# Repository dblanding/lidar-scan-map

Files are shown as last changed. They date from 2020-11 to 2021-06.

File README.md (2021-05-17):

## Mapping LiDAR scan data
This project uses a Benewake TFMini Plus LiDAR module mounted to scan 225 degrees on a vertical axis. A hall effect angle encoder reports the angular position of the scan rotor.

### Rotating LiDAR mounted on a Zero Turn (early prototype) car:
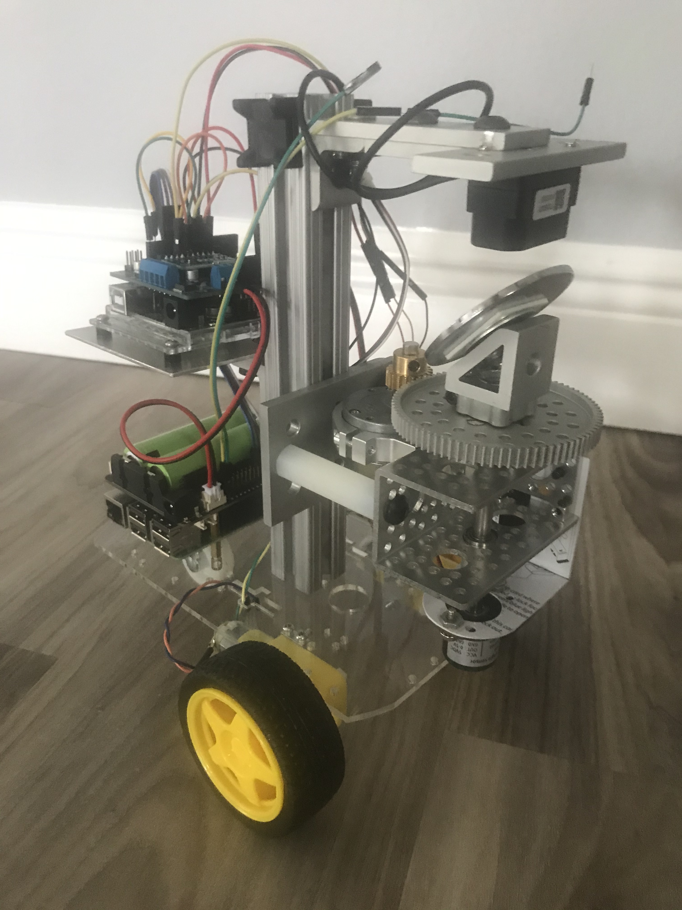
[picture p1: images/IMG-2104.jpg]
Zero Turn Car with rotating LiDAR


### Rotating LiDAR mounted on an Omni-Wheel type car:
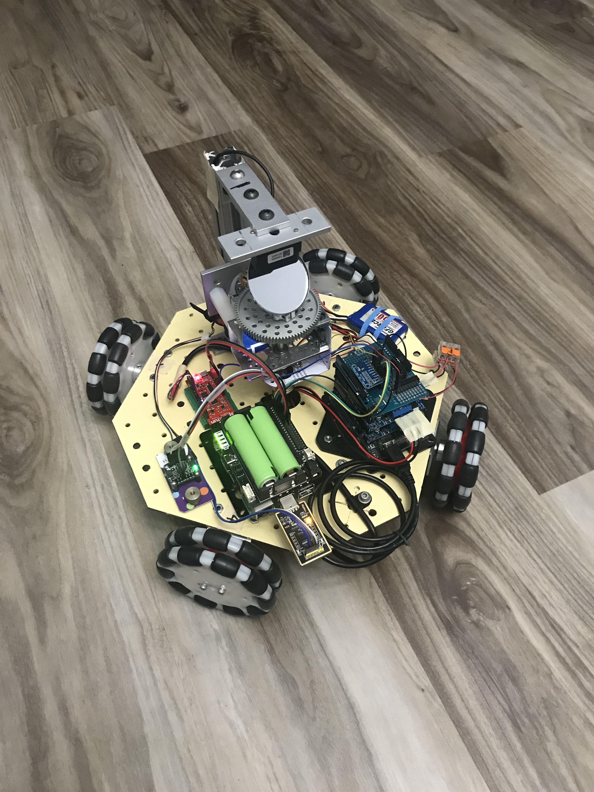
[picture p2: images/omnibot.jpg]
Omni Wheel Car with rotating LiDAR


More about **Omni-Wheels** can be found [here](omni-wheels.md).

By using the scan data, the car can navigate autonomously,
able to make a [multi-leg trip](docs/triplog-21-05-16-06-00/trip_log.md) through the house.  
An onboard Raspberry Pi 3B+ runs a python program which:  
* Collects data from the TFminiPlus on a USB serial port
* Collects readings from the angular encoder via ADC (on I2C bus)
* Finds the best fit lines through the scan points
* Displays a plot of the points and the best fit lines.
* Using OpenCV, calculates the best path forward, avoiding objects in its environment
* Sends motor drive commands to the Arduino on the serial port  
  (Arduino controls the motors through an Adafruit motor shield)
* Keeps track of its position using data from an IMU and an odometer.
  * The IMU is an Adafruit BNO085 operating in RVC mode, sending data via serial
  * The odometer is a wheel mounted on the shaft of an incremental encoder,
    * Encoder data is collected by an ESP32 and sent to RasPi via ADC

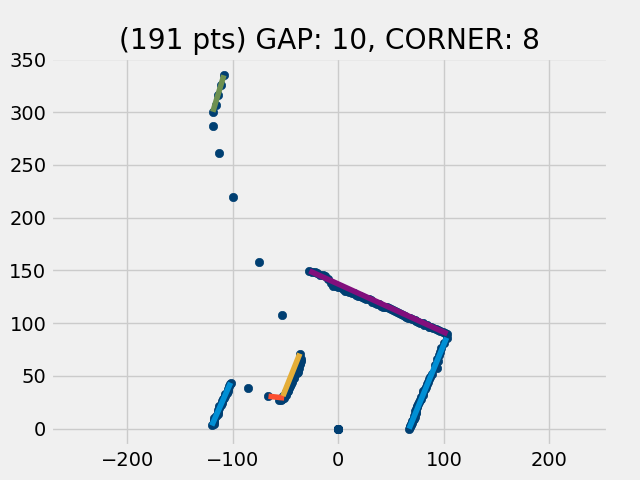
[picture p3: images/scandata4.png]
plot showing data points & best-fit lines


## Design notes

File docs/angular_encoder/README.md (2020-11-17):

### Investigate use of ADS1115 ADC to collect angle encoder data

Started with [Adafruit ADS1x15 Library](https://learn.adafruit.com/raspberry-pi-analog-to-digital-converters/ads1015-slash-ads1115) to convert 0-5v signal from angle encoder to digital value and send it to the RasPi via I2C bus. This worked quite well. The Python program ads1115speedTest.py shows that encoder values can be received at rates easily exceeding the 100Hz speed of the TFminiPlus.
#### Calibration:

I conducted a calibration procedure in which the angle encoder was positioned at 90, 180, and 270 degrees. (Actually, I hooked up a meter to the output of the encoder and positioned it at 1.25V, 2.5V, and 3.75V) then used the python prgogram to get the encoder value.)
Along the way, I discovered a couple of  things:
* >One problem I discovered was that different 5V power supplies are not always exactly 5V.
When the Geekworm X728 UPS is plugged in and charging, the RasPi 5V level goes to 5.25V.
When it's unplugged it drops to more nearly 5V.
If an Arduino is hooked to the RasPi by USB, The Arduino 5V level is similarly affected, but not as severly. It goes from 5.1V when the X728 is charging to 4.95V when the charger is unplugged. 
* >I chose to use the Arduino power supply because it is the best one available. The [ADS1115 datasheet](https://cdn-shop.adafruit.com/datasheets/ads1115.pdf) explains that at its default settings, it converts a voltage between -4.096V and +4.096V to a number that ranges from -32768 to 32767. With these default settings, useful values are gotten in the desired angular range (90 degrees to 270 degrees).
* >Using the Arduino 5V supply (and with the charger unplugged) I manually moved the rotor to each of 3 positions: 1.25V, 2.50V, 3.75V and recorded the corresponding encoder count value. To achieve the best agreement between the measured encoder count value and the calculated encoder count value, I ended up fudging the 4.096 number to 4.115. See Excel file ang_encdr_calibr.xlsx  
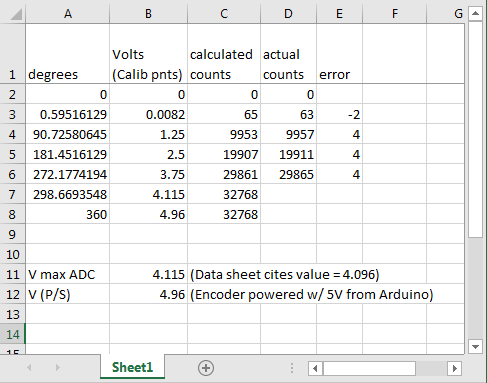
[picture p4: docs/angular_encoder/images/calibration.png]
Excel sprreadsheet


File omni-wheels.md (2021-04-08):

## OMNI-WHEEL CAR

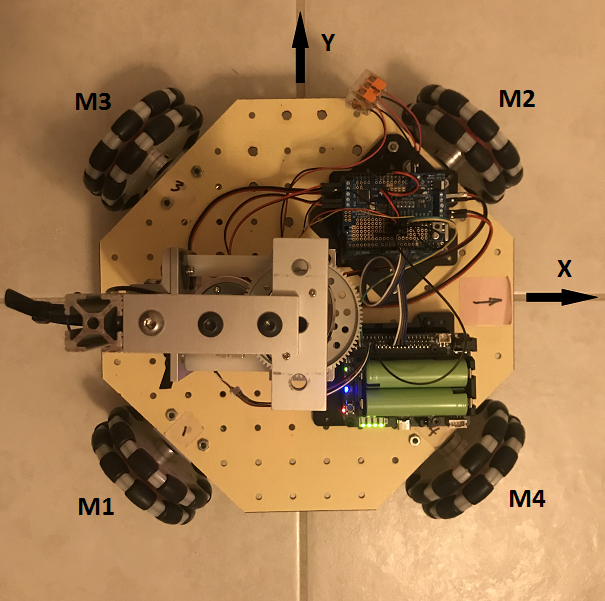
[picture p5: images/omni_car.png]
omni-wheel car


### Top view of Omni Wheel car showing wheel/motors and directional conventions

This configuration of omni-wheels is easily controlled to move in any direction: X, Y, θz:
- forward-back motion (along the X axis)
- right-left sideways motion (along the Y axis)
- spin motion (θz).

Moreover, all three of these motions can be superimposed. The motors can be commanded to combine these motions simultaneously. (More about that later.) For now, let's just consider how we can get the car to move in one DOF at a time.

Imagine that we want to drive the car along a -45 degree direction into the fourth quadrant (along the common axis of wheel motors M3 and M4). Only wheel motors **M1 and M2** would run. **M1** would need to be driven **clockwise** and **M2** would need to be driven **CCW** at the same speed. Wheel motors M3 and M4 would not run. To drive drive the car at speed S along the 45 degree direction, we would send the following drive values to the motors:

```
m1 = +S
m2 = -S
m3 = 0
m4 = 0
```

Now imagine that we want to drive the car along a +45 degree direction into the first quadrant (along the common axis of wheel motors M1 and M2). Only wheel motors **M3 and M4** would run. **M4** would need to be driven **clockwise** and **M3** would need to be driven **CCW** at the same speed. Wheel motors M1 and M2 would not run. To drive drive the car at speed S along the 135 degree direction, we would send the following drive values to the motors:

```
m1 = 0
m2 = 0
m3 = -S
m4 = +S
```

Notice that the car's motion along the -45 degree direction is completely **independent** from its motion along the **orthogonal** +45 degree direction. First, it suggests that the "natural coordinate system" for the omni-wheels runs through the wheel axes (which happens to be oblique to the car's coordinate system). But it also invites us to realize that we may combine the control of these two **independent degrees of freedom** in any combination we desire. Thus, it seems reasonable to consider driving the car in any arbitrary angular direction. The mathematics of this is simplified by using **polar coordinates (r, θ)** to specify the speed and direction of the car. To convert between the omni-wheels 'natural' coordinates and the car's coordinates, we simply add or subtract 45 degrees (pi/4) from the theta value. Below is the algorithm to drive the car in a direction theta at speed.

```
speed, theta = desired_speed_and_direction
theta -= pi/4
u, v = convert_polar_to_rect(speed, theta)
m1 = u
m2 = -u
m3 = -v
m4 = v
```
Notice the rectangular coordinates in the omni-wheel's natural coordinate system have been labeled u, v. This is intended to remind us that they are not the same as x, y coordinates in the car's coordinate system.
If we want to simultaneously spin the car **CCW** about its own Z axis, all four wheel motors would receive an additional **CW** component as shown below.
```
spin = some_value
speed, theta  = desired_speed_and_direction
theta -= pi/4
u, v = convert_polar_to_rect(speed, theta)
m1 = u + spin
m2 = -u + spin
m3 = -v + spin
m4 = v + spin
```

### Maintaining Cross-Track position within travel lane

Let's say we want our omni-wheel car to travel forwrd (FWD) in the positve X direction and we want it to stay centered in its travel lane. Just like any car, it is neccesary to make subtle steering corrections in response to unintended cross-track deviations from its intended path. In the figure below, our car has been shown in a 'travel lane' traveling from left to right. 

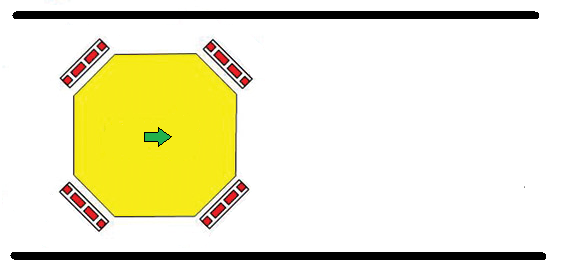
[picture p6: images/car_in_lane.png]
car in lane


This is where polar coordinates again come to the rescue. It's easy to make a subtle steering correction if we're already working in polar coordinates. Simply modulate the angle coordinate until the car's cross-track position error has been nulled. Done!
Below is shown the signature of the method to drive the car using polar coordinates. 

``` python
    def go(self, speed, angle, spin=0):
        """
		Drive at speed (int) in relative direction angle (degrees)
        while simultaneoulsy spinning CCW at rate = spin (int).
        """
```

### Making radius turns

What if the lane is curved? How do we make the car follow a curved path of radius = R as shown in the diagram below? That's what the spin parameter is for.

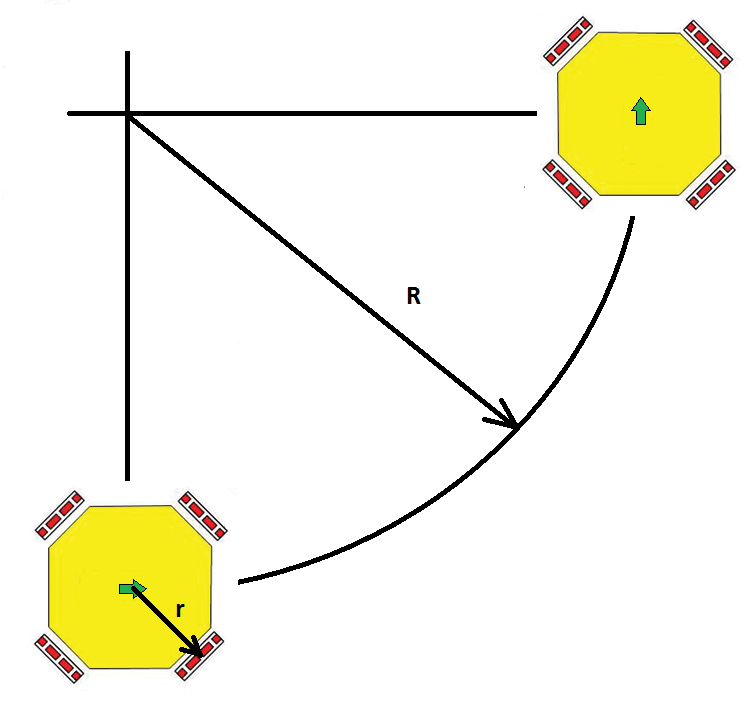
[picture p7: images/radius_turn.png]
curved path


This diagram shows our car moving in the FWD direction while simultaneously spinning CCW, resulting in a path which is the arc of a circle of radius R. We need to come up with the correct value of spin which will produce 90 degrees of rotation as the car translates along 1/4 of the circumference of the circle.

Notice that the drive direction of the wheels is 45 degrees from the direction of travel of the car. As a result, the motion of the wheels at their interface with the floor must **exceed** the distance the car translates by a factor of √2.

> translation distance (at wheels) = (pi * R/2) * √2

Knowing the dimension r from the car's geometric center to each wheel, we can find the corresponding value of spin that will produce 90 degrees of CCW rotation of the car about its own axis is:

> spin distance (at wheels) = pi * r/2

In summary, the car will follow the curved path of radius R if the value of spin is proportional to the car speed in the following ratio:

> spin_ratio =  r/R * √2/2

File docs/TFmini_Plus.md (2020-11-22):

## TF Mini / TF Mini Plus resources

[Benewake website](http://en.benewake.com/)

### TF Mini

The TFmini is available in two different comm. configurations: I2C & Serial.
The one I have is the Serial type and cannot work in I2C mode.

[Instructables (Complete guide)](https://www.instructables.com/Benewake-LiDAR-TFmini-Complete-Guide/)

[Sparkfun tutorial (I2C)](https://learn.sparkfun.com/tutorials/tfmini---micro-lidar-module-qwiic-hookup-guide)

[Sparkfun tutorial (UART)](https://learn.sparkfun.com/tutorials/tfmini---micro-lidar-module-hookup-guide)

### TF Mini Plus

The TFMini-Plus works optionally in either serial or I2C mode.

[Benewake TFmini_Plus README](https://github.com/TFmini/TFmini-Plus/blob/master/README.md)

[Arduino library for TFMini-Plus using I2C interface](https://github.com/budryerson/TFMini-Plus-I2C)

[Medium article: Interfacing TFmini Plus LiDAR with Raspberry Pi](https://medium.com/@engribrahimqazi/interfacing-tfmini-plus-lidar-with-raspberry-pi-4b-6cd82fcca5f1)

> This last article led me to discover that the TF Mini can send its data directly to the RasPi Python program. No need for an Arduino.  
Instead of using the Arduino to interface with the lidar and then send the data to my python program over the serial bus, I should allow the Python program to interface directly with the TFmini Plus. I took the code in the article and modified it so it doesn't waste time printing, but just collects data as fast as it arrives on the serial port.

```
# -*- coding: utf-8 -*
"""from 'Interfacing TFmini Plus LiDAR with Raspberry Pi 4B' by Ibrahim Qazi
https://medium.com/@engribrahimqazi/interfacing-tfmini-plus-lidar-with-raspberry-pi-4b-6cd82fcca5f1

Needed to enable serial through gpio pins by doing the following:
First: sudo raspi-config, Interfacing Options, then Serial,
select No for the login shell and Yes for the serial port hardware to be enabled.
Afterwards, reboot.
Change serial device from "/dev/ttyAMA0" to "/dev/ttyS0".
"""

import time
import serial

ser = serial.Serial("/dev/ttyS0", 115200)

def read_data():
    """Read data from Benewake TFmini Plus LiDAR and print it"""
    last_time = time.time()
    data = []
    while len(data) < 100:
        counter = ser.in_waiting # count the number of bytes of the serial port
        if counter > 8:
            bytes_serial = ser.read(9)
            
            if bytes_serial[0] == 0x59 and bytes_serial[1] == 0x59:
                distance = bytes_serial[2] + bytes_serial[3]*256
                strength = bytes_serial[4] + bytes_serial[5]*256
                temperature = bytes_serial[6] + bytes_serial[7]*256
                temperature = (temperature/8) - 256
                now = time.time()
                strline = "%s, %s, %s, %s, %s\n" % (counter, distance, strength,
                                                    temperature, now - last_time)
                data.append(strline)
                last_time = now
    with open('tfminiPlus_data', 'w') as f:
        print(len(data))
        f.writelines(data)

if __name__ == "__main__":
    if ser.isOpen() == False:
        ser.open()
    read_data()
```

Examination of the output file, shows that a read occurs as soon as 9 bytes are queued up and waiting on the serial port.  
Also, the elapsed time since the previous read hovers right around 10 mSec, so the device really does operate at 100 Hz, as advertised. 

Bytes waiting, distance, strength, temperature, time since last read

```
9, 28, 5812, 60.0, 0.001964092254638672
9, 28, 5814, 60.0, 0.010060310363769531
9, 28, 5815, 60.0, 0.010145902633666992
9, 28, 5821, 60.0, 0.010141611099243164
9, 28, 5813, 60.0, 0.010251522064208984
9, 28, 5818, 60.0, 0.010085821151733398
9, 28, 5818, 60.0, 0.010092496871948242
9, 28, 5819, 60.0, 0.010134696960449219
9, 28, 5816, 60.0, 0.010140180587768555
9, 28, 5812, 60.0, 0.010195255279541016
9, 28, 5821, 60.0, 0.010090112686157227
...
```

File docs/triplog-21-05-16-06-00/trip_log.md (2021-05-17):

## Log for Trip started Sun May 16 06:00:17 2021.  
  
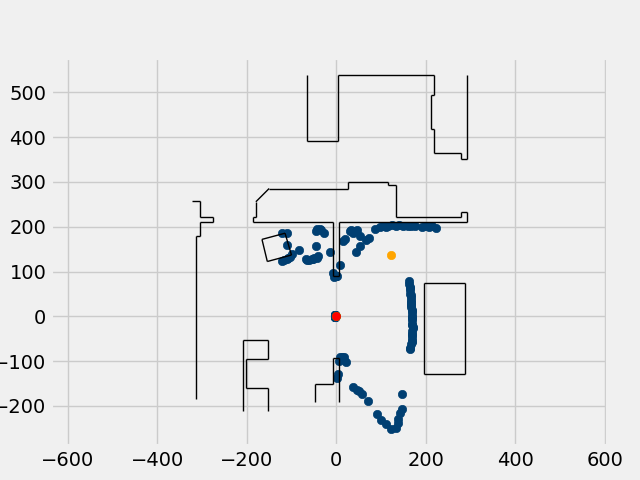
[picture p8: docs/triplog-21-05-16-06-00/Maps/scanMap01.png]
Map Plot 01
  
Leg 1  
Starting Coords: (0, 0)  
Turning Left 48.0 deg to heading -48.01  
Heading after turn: -48.57 deg.  
Distance to target: 184.0 cm.  
Distance driven: 176 cm.  
Heading after drive: -48.230000000000004 deg.  
Ending Coords: (118, 130)  
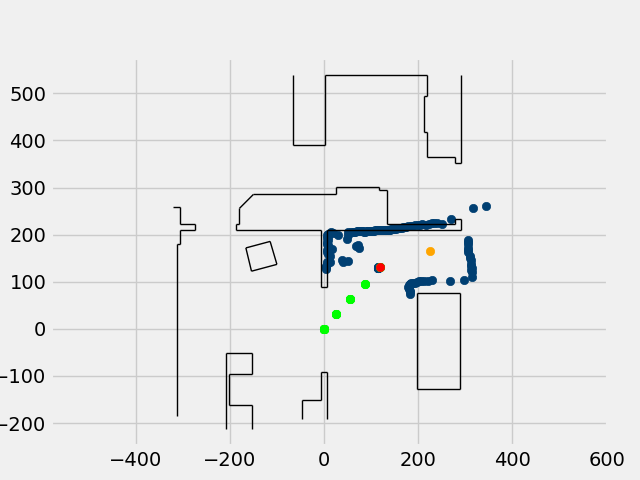
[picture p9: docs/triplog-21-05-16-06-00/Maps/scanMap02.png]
Map Plot 02
  
Leg 2  
Starting Coords: (118, 130)  
Turning Right 29.999999999999996 deg to heading -18.250000000000004  
Heading after turn: -16.65 deg.  
Distance to target: 112.0 cm.  
Distance driven: 115 cm.  
Heading after drive: -13.56 deg.  
Ending Coords: (228, 163)  
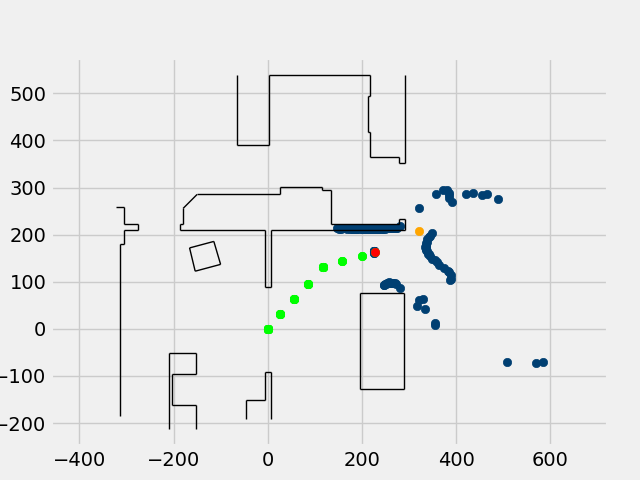
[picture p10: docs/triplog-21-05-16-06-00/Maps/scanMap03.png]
Map Plot 03
  
Leg 3  
Starting Coords: (228, 163)  
Turning Left 11.999999999999998 deg to heading -25.57  
Heading after turn: -23.740000000000002 deg.  
Distance to target: 103.0 cm.  
Distance driven: 103 cm.  
Heading after drive: -21.94 deg.  
Ending Coords: (322, 205)  
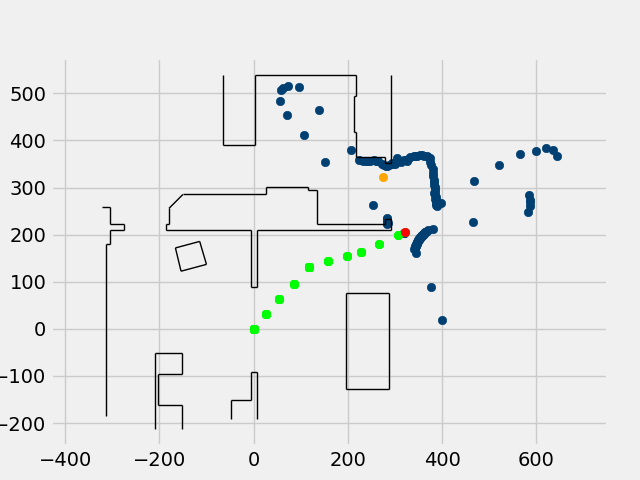
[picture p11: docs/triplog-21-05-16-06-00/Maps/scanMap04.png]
Map Plot 04
  
Leg 4  
Starting Coords: (322, 205)  
Turning Left 90.0 deg to heading -111.94  
Heading after turn: -108.47 deg.  
Distance to target: 127.0 cm.  
Distance driven: 129 cm.  
Heading after drive: -108.81 deg.  
Ending Coords: (279, 326)  
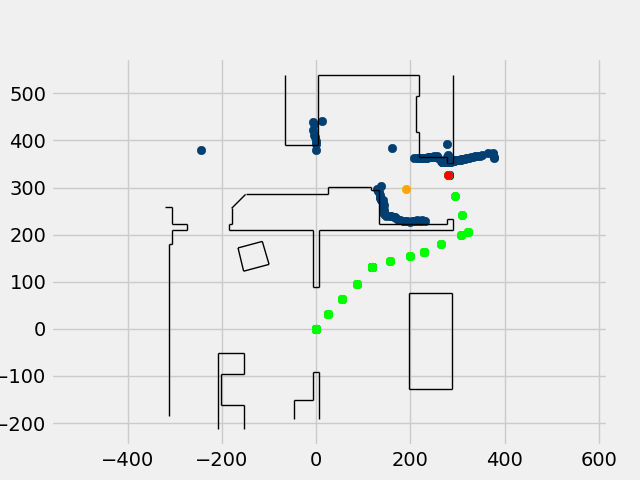
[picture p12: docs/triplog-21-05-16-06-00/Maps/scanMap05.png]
Map Plot 05
  
Leg 5  
Starting Coords: (279, 326)  
Turning Left 90.0 deg to heading -198.79000000000002  
Heading after turn: 161.45000000000002 deg.  
Distance to target: 94.0 cm.  
Distance driven: 84 cm.  
Heading after drive: 161.48 deg.  
Ending Coords: (201, 297)  
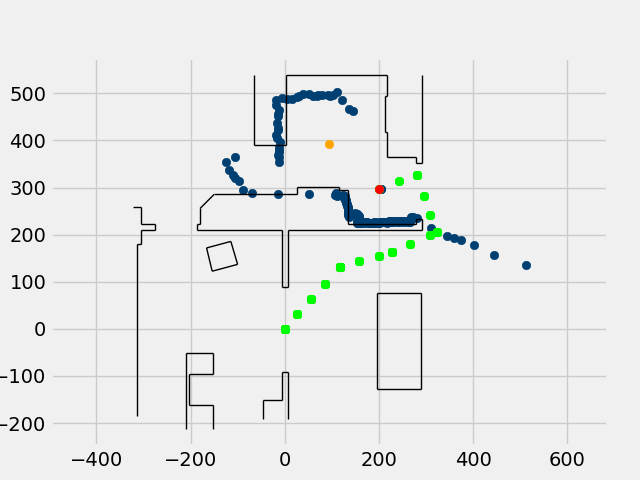
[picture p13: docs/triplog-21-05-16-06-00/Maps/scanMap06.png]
Map Plot 06
  
Leg 6  
Starting Coords: (201, 297)  
Turning Right 59.99999999999999 deg to heading 221.5  
Heading after turn: -140.25 deg.  
Distance to target: 142.0 cm.  
Distance driven: 143 cm.  
Heading after drive: -137.70000000000002 deg.  
Ending Coords: (91, 389)  
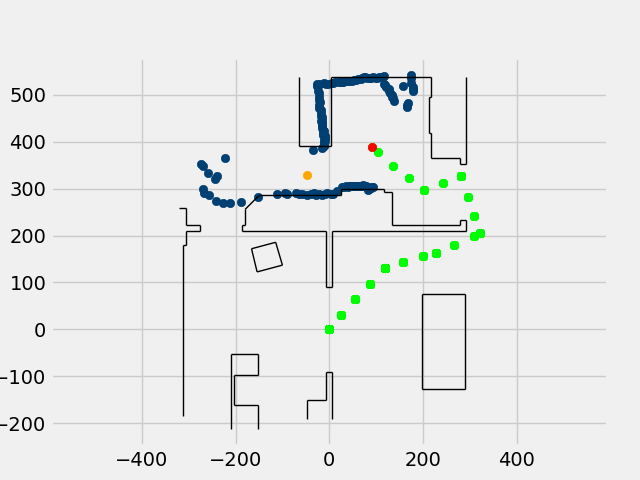
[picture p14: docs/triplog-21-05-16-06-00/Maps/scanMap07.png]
Map Plot 07
  
Leg 7  
Starting Coords: (91, 389)  
Turning Left 66.0 deg to heading -203.66  
Heading after turn: 156.94 deg.  
Distance to target: 152.0 cm.  
Distance driven: 146 cm.  
Heading after drive: 158.76 deg.  
Ending Coords: (-40, 326)  
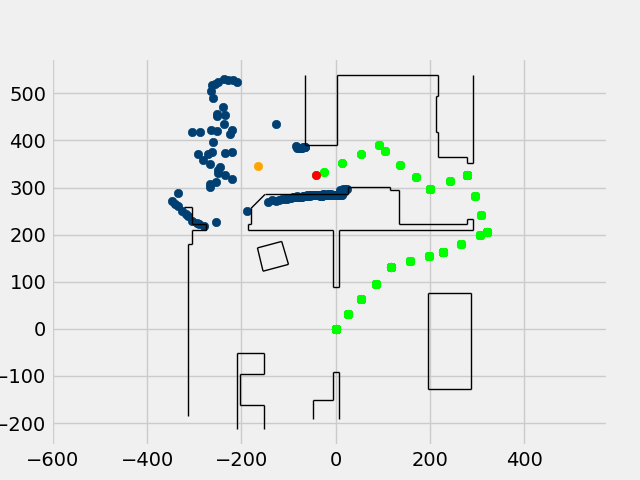
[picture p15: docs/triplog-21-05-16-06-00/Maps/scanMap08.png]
Map Plot 08
  
Leg 8  
Starting Coords: (-40, 326)  
Turning Right 29.999999999999996 deg to heading 188.75  
Heading after turn: -173.33 deg.  
Distance to target: 125.0 cm.  
Distance driven: 128 cm.  
Heading after drive: -170.89000000000001 deg.  
Ending Coords: (-167, 342)  
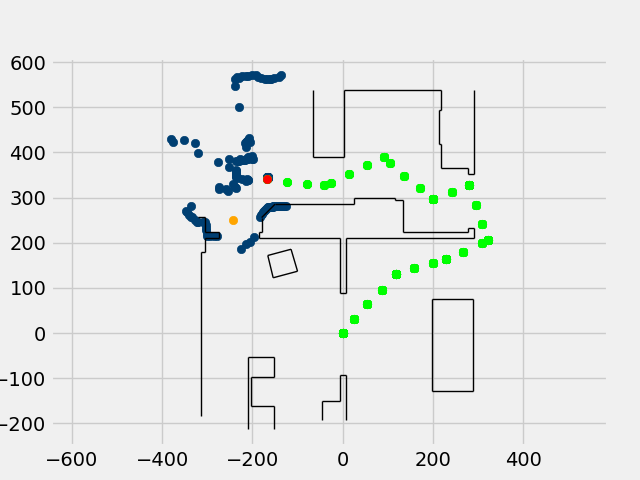
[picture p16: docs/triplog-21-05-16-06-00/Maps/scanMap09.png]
Map Plot 09
  
Leg 9  
Starting Coords: (-167, 342)  
Turning Left 59.99999999999999 deg to heading -230.86  
Heading after turn: 131.03 deg.  
Distance to target: 118.0 cm.  
Distance driven: 117 cm.  
Heading after drive: 129.8 deg.  
Ending Coords: (-242, 251)  
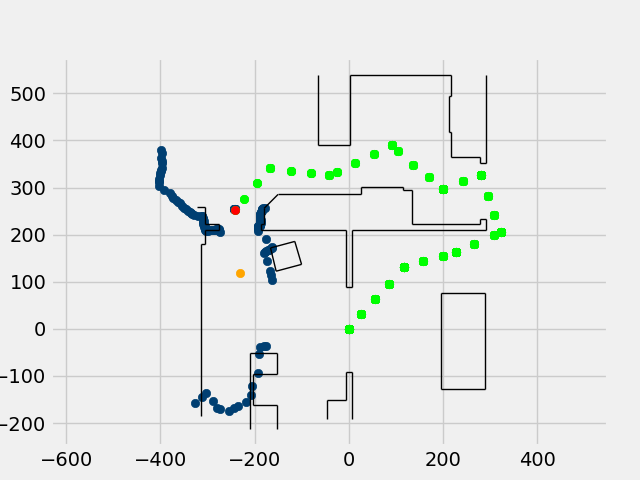
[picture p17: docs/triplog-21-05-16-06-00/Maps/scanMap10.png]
Map Plot 10
  
Leg 10  
Starting Coords: (-242, 251)  
Turning Left 45.0 deg to heading 84.81  
Heading after turn: 88.05 deg.  
Distance to target: 134.0 cm.  
Distance driven: 130 cm.  
Heading after drive: 86.9 deg.  
Ending Coords: (-234, 121)  
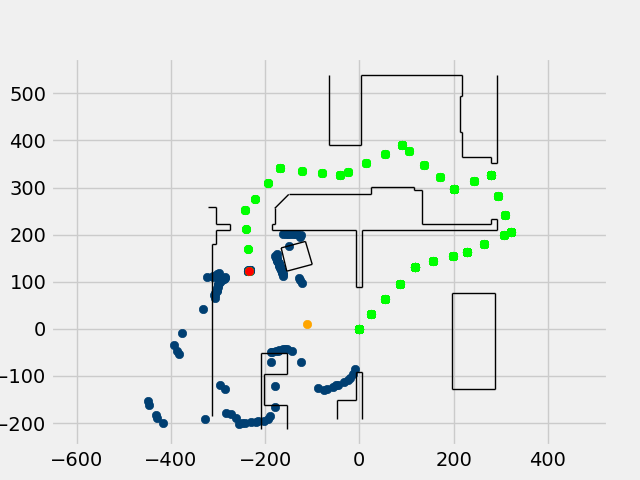
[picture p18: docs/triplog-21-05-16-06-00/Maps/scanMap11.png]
Map Plot 11
  
Leg 11  
Starting Coords: (-234, 121)  
Turning Left 45.0 deg to heading 41.900000000000006  
Heading after turn: 42.5 deg.  
Distance to target: 166.0 cm.  
Distance driven: 164 cm.  
Heading after drive: 44.27 deg.  
Ending Coords: (-112, 11)  
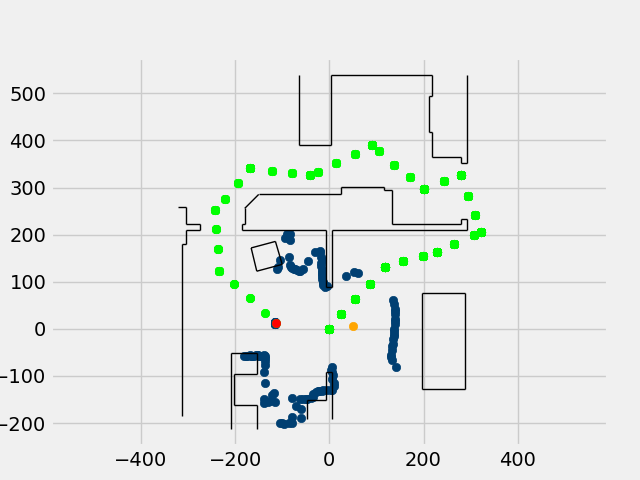
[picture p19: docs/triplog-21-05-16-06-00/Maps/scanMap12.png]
Map Plot 12
  
Leg 12  
Starting Coords: (-112, 11)  
Turning Left 42.0 deg to heading 2.240000000000002  
Heading after turn: 1.0 deg.  
Distance to target: 164.0 cm.  
Distance driven: 161 cm.  
Heading after drive: 1.02 deg.  
Ending Coords: (48, 15)  
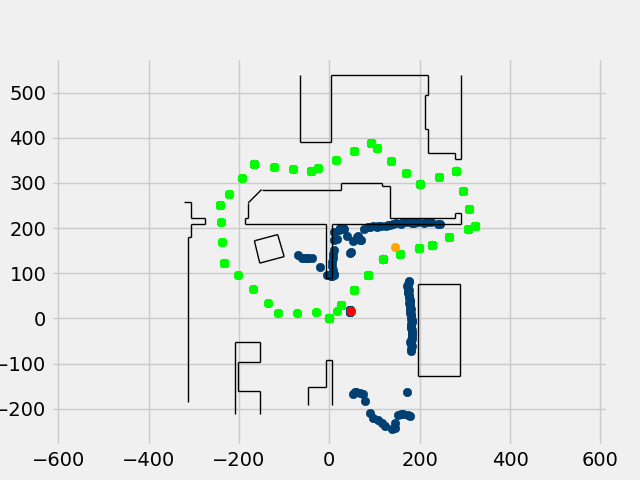
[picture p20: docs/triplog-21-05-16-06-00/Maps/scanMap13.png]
Map Plot 13
  
Leg 13  
Starting Coords: (48, 15)

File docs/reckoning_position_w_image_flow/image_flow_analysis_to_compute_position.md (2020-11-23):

## Can image flow analysis of consecutive scans be used instead of encoders to keep track of robot position?
### 11/23/2020
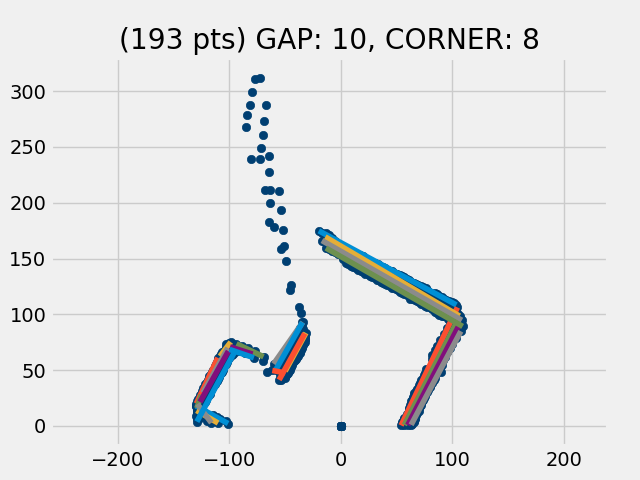
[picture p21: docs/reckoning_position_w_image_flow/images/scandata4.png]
robot moved through 4 positions separated by 2 in


The image above shows 4 scans overlayed as the robot is advanced through 4 positions along the Y axis spaced roughly 2 inches apart. The units on the X and Y axes are in cm, by the way.

The question is: Can we do an **image flow analysis** (similar to the way an optical mouse works) to make a reasonable calculation of the change in the robot's position as it advances from one position to the next.

It looks as though it should be possible. This would simplify the robot as it would be unneccesary to keep track of its position using the usual encoders and/or stepper motors.

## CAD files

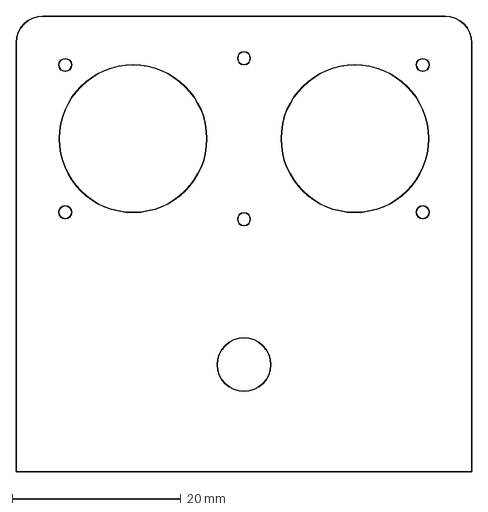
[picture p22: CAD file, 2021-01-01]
CAD/HC-SR04_CC_mnt.dxf
53.9 x 54.0 mm

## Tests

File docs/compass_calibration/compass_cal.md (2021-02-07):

## Compass Calibration

I wanted to see if the uncorrected data I was getting from the HMC5883L device on the robot was in good agreemeent with the compass app on my phone. It wasn't. Here is what I found just looking at the cardinal directions:

Device	 | North | East | South | West
-------- | ----- | ---- | ----- | ----
TRUE     |   0   |  90  |  180  |  270
Phone    |   0   |  87  |  186  |  278
HMC5883L |  113  |  205 |  267  |  333

What I found was the values from the HMC5883L device were absolutely horrible and the phone was actually pretty far off too (although nowhere near as bad).

Next, I set up a turntable and collected data at 10 degree intervals. I used my phone to set the North diection, then placed the robot on the turntable as shown in the picture below.

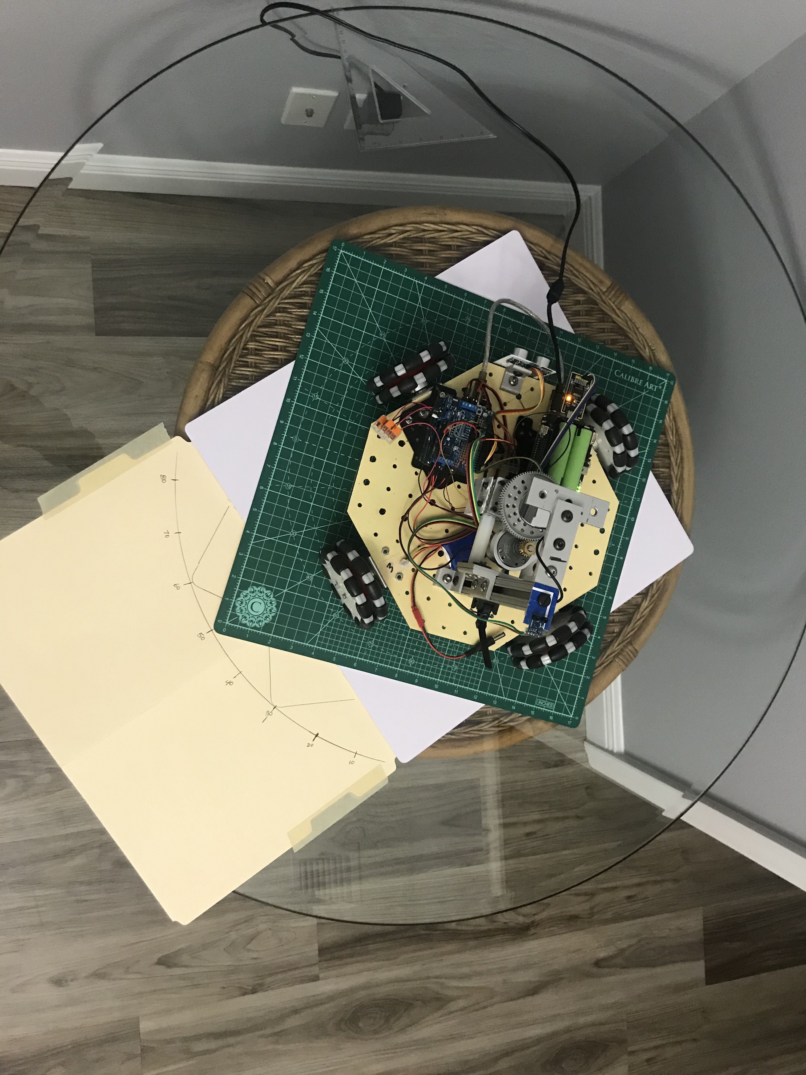
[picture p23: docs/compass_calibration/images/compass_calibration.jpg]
Robot on Turntable


I used this setup to collect values from the HMC5883L every 10 degrees. 

True     | Compass
--------- | --------
-60 | 6
-50 | 21
-40 | 37
-30 | 57
-20 | 76
-10 | 96
0 | 114
10 | 129
20 | 141
30 | 152
40 | 163
50 | 173
60 | 181
70 | 190
80 | 198
90 | 206
100 | 213
110 | 220
120 | 227
130 | 234
140 | 241
150 | 248
160 | 254
170 | 261
180 | 268
190 | 274
200 | 281
210 | 287
220 | 294
230 | 301
240 | 309
250 | 316
260 | 325
270 | 334
280 | 343
290 | 354
300 | 6
310 | 21
320 | 37
330 | 57
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

I then used [Excel](compass_data.xlsx) to plot the data and discovered that it was pretty non-linear. Empirically, values were found for the magnitude and phase of a sine wave that did a pretty good job of linearizing the data. By subtracting the sine wave and an additional fixed offset, the HMC5883L data could be corrected to a point where it was within a degree or two of the "True" direction over the entire range of values. 

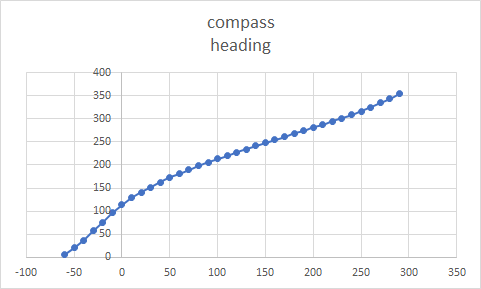
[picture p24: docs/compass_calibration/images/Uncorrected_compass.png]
Uncorrected Compass Data


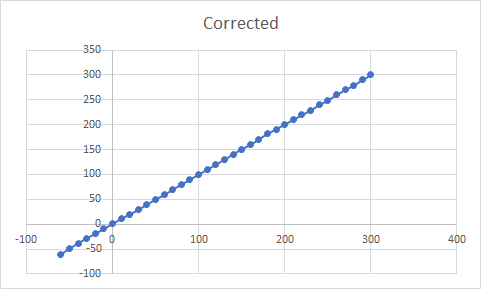
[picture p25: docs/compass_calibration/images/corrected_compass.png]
Corrected Compass Data


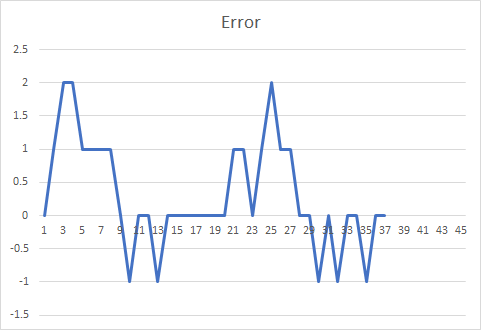
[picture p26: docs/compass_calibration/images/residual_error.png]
Residual Error


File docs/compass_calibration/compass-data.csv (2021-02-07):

True Heading | compass heading | 30 | 164 |  | Corrected | Error
-60 | 6 | -27.81548946 | 33.81548946 | 3.81548946 | -60 | 0
-50 | 21 | -23.95902724 | 44.95902724 | 14.95902724 | -49 | 1
-40 | 37 | -18.05440584 | 55.05440584 | 25.05440584 | -38 | 2
-30 | 57 | -8.771105887 | 65.77110589 | 35.77110589 | -28 | 2
-20 | 76 | 1.047023797 | 74.9529762 | 44.9529762 | -19 | 1
-10 | 96 | 11.23822569 | 84.76177431 | 54.76177431 | -9 | 1
0 | 114 | 19.28364523 | 94.71635477 | 64.71635477 | 1 | 1
10 | 129 | 24.57457021 | 104.4254298 | 74.42542979 | 11 | 1
20 | 141 | 27.61514958 | 113.3848504 | 83.38485042 | 20 | 0
30 | 152 | 29.34442913 | 122.6555709 | 92.65557087 | 29 | -1
40 | 163 | 29.99543086 | 133.0045691 | 103.0045691 | 40 | 0
50 | 173 | 29.63065084 | 143.3693492 | 113.3693492 | 50 | 0
60 | 181 | 28.68914488 | 152.3108551 | 122.3108551 | 59 | -1
70 | 190 | 26.96382643 | 163.0361736 | 133.0361736 | 70 | 0
80 | 198 | 24.87113559 | 173.1288644 | 143.1288644 | 80 | 0
90 | 206 | 22.29435719 | 183.7056428 | 153.7056428 | 90 | 0
100 | 213 | 19.68178723 | 193.3182128 | 163.3182128 | 100 | 0
110 | 220 | 16.77580764 | 203.2241924 | 173.2241924 | 110 | 0
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

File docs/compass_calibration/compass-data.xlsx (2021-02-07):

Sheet: uncorrected
True Heading | compass heading
-60 | 6
-50 | 21
-40 | 37
-30 | 57
-20 | 76
-10 | 96
0 | 114
10 | 129
20 | 141
30 | 152
40 | 163
50 | 173
60 | 181
70 | 190
80 | 198
90 | 206
100 | 213
110 | 220
120 | 227
130 | 234
140 | 241
150 | 248
160 | 254
170 | 261
180 | 268
190 | 274
200 | 281
210 | 287
220 | 294
230 | 301
240 | 309
250 | 316
260 | 325
270 | 334
280 | 343
290 | 354
300 | 6
310 | 21
320 | 37
330 | 57
340 | 76
350 | 96
360 | 114

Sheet: compass-data-linearized
True Heading | compass heading | COS term | Subtract cos term | Subtract Offset | Corrected | Error
 |  | 30 | 164
-60 | 6 | -27.81548946 | 33.81548946 | 3.81548946 | -60 | 0
-50 | 21 | -23.95902724 | 44.95902724 | 14.95902724 | -49 | 1
-40 | 37 | -18.05440584 | 55.05440584 | 25.05440584 | -38 | 2
-30 | 57 | -8.771105887 | 65.77110589 | 35.77110589 | -28 | 2
-20 | 76 | 1.047023797 | 74.9529762 | 44.9529762 | -19 | 1
-10 | 96 | 11.23822569 | 84.76177431 | 54.76177431 | -9 | 1
0 | 114 | 19.28364523 | 94.71635477 | 64.71635477 | 1 | 1
10 | 129 | 24.57457021 | 104.4254298 | 74.42542979 | 11 | 1
20 | 141 | 27.61514958 | 113.3848504 | 83.38485042 | 20 | 0
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

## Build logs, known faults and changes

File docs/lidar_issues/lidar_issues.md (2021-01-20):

## Lidar issues

I have the TFmini Plus LiDAR module (model/serial: T250025 0012937) attached to the Raspberry Pi model 3B+ using the Python 3 code found at [Interfacing TFmini Plus LiDAR with Raspberry Pi 4B](https://github.com/ibrahimqazi/TFmini-Plus-LiDAR-interfacing-with-Raspberr-Pi).

Initially, I have the LiDAR module attached to a USB serial adapter which uses serial port /dev/ttyUSB0.

Scanning is accomplished by mounting a tilted mirror on a rotor which is made to spin about a vertical axis. This allows the LiDAR module to be mounted in a fixed position. An angle encoder mounted on the rotor axis provides directional data.

Below are the first 21 lines of data collected (There are actually 109 lines in the entire 180 degree scan). Each line has 2 values: the encoder value and the distance in cm measured by the LiDAR.

```
10521,0
10708,196
10888,196
11063,196
11209,191
11425,191
11598,191
11781,180
11949,180
12142,180
12320,173
12498,173
12678,173
12852,197
13035,197
13192,230
13390,230
13574,230
13752,239
13936,239
14124,239
```
Notice that the encoder values go up steadily, but the distance values change only every 3rd line (occasionally 2nd line). The result is that only about 1/3 of the data is meaningful. I end up throwing away almost 2 of every 3 data points. After throwing out the redundant points (and points that have distance values of 0 or 1200), the plot below is generated. Notice that it has only 27 points.

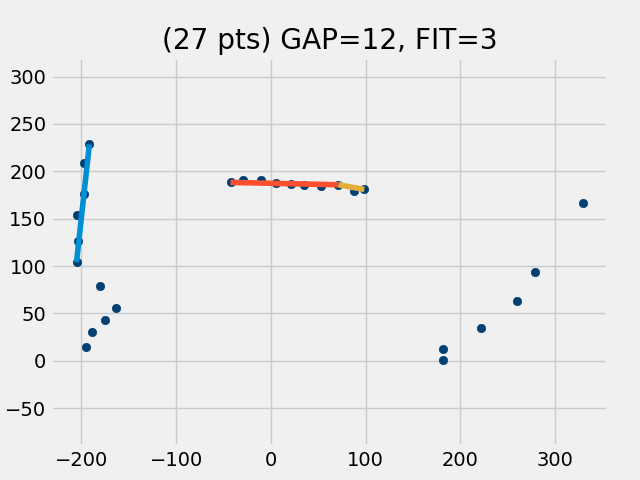
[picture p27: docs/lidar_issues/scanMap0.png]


So what could be causing the LiDAR to give these redundant values? Maybe it is the LiDAR module itself. So I replaced the module with a newer one (model/serial: T260051 0011907). Here are the first 20 lines of scan data  (also 109 lines long). Looks like it has the same problem with triplets and the occasional twin.

```
10486,0
10667,0
10821,0
11033,154
11216,154
11406,154
11588,150
11771,150
11951,150
12130,151
12310,151
12482,151
12662,169
12841,169
12994,169
13203,178
13406,178
13595,212
13795,212
13989,212
```

From the data above, it is clear that this did not remedy the data triplet problem. Not surprisingly, the resulting plot shows a similar reduction of the number of data points. 

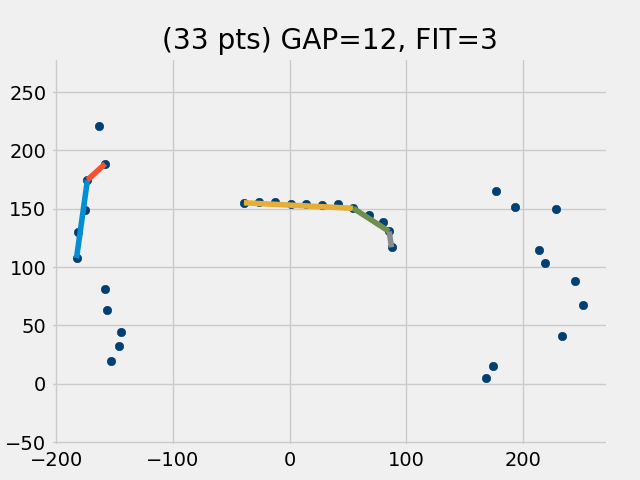
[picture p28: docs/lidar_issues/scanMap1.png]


OK, changing to a newer module didn't solve the problem. Maybe the problem is being caused in transit on the serial bus. 

To explore this, I modified my setup to connect the TFmini Plus to the Raspberry Pi's builtin UART on pins 6 & 8 (instead of the USB Serial adapter).

Here are the first 20 lines of scan data (total = 107 lines this time). Now there are no data triplets (but there are lots of twins).
```
10570,263
10784,140
10978,139
11178,139
11365,163
11550,163
11732,170
11918,170
12099,194
12282,204
12473,204
12649,212
12841,212
13029,219
13199,219
13406,224
13588,232
13774,232
13952,239
14137,239
```
This makes a very noticeable difference in the resulting plot. 

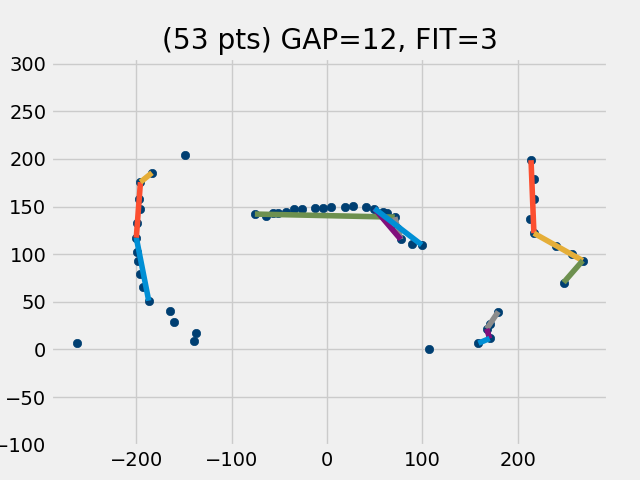
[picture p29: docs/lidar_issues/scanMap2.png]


Unfortunately however, the **shapes** of the scanned objects are distorted in the above plot. For example, the object that lies straight ahead of the scanner (on the vertical grid line labeled '0') is distorted. It is the back of a sofa and it is actually straight. So now I want to replace the LiDAR module with the original one, but still leave it attached to the RasPi's built-in serial port. Below is shown the resulting plot. This is how the back of the sofa is **really supposed to look**. Notice also that the wall at the left is straight. It is supposed to be straight. Apparently there is something going on with the new LiDAR module that is not quite right.

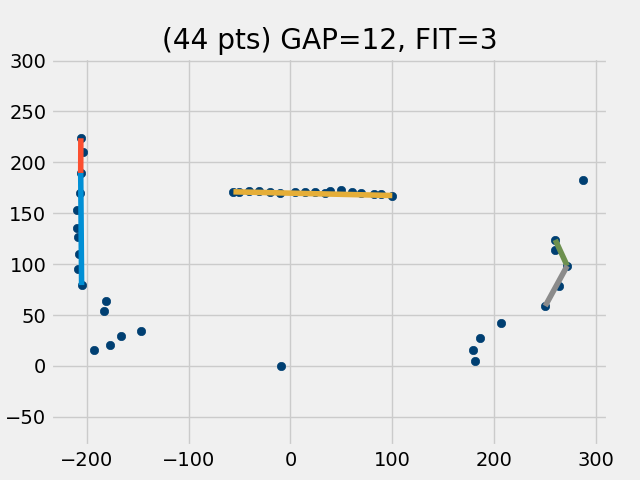
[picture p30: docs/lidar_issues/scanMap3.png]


## Problem Found (and resolved)!

#### The problem

Looking at the raw scan data shows the problem is being caused by reading the serial bus **too frequently and whether or not there is new data available to be read**. And to make matters worse, every time the method is called, the input buffer is reset, further delaying the acquisition of new data.

#### The solution

The read_dist method has now been revised to wait until 9 bytes have accumulated on the input buffer, then it reads the data. The input buffer is not reset so no data is thrown away. Below is a scan with the new read_dist method, using the original LiDAR module, attached to the USB serial port. This is actually a pretty accurate representation of the room.

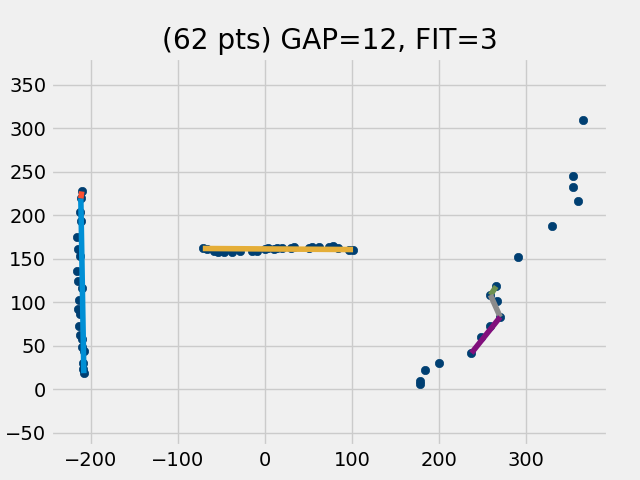
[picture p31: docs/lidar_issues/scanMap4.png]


```    def read_dist(self):
        """Set self.distance = distance (cm) read from lidar module.
        Return number of bytes waiting on serial port when read.
        """
        # Prior to first read, purge buildup of 'stale' data
        if ser1.in_waiting > 100:
            ser1.reset_input_buffer()

        # Wait for serial port to accumulate 9 bytes of 'fresh' data
        while ser1.in_waiting < 9:
            time.sleep(.0005)

        # Now read 9 bytes of data on serial port
        counter = ser1.in_waiting
        bytes_serial = ser1.read(9)
        if bytes_serial[0] == 0x59 and bytes_serial[1] == 0x59:
            self.distance = bytes_serial[2] + bytes_serial[3]*256
            #self.strength = bytes_serial[4] + bytes_serial[5]*256
            #temperature = bytes_serial[6] + bytes_serial[7]*256
            #self.temperature = (temperature/8) - 256
        return counter
```

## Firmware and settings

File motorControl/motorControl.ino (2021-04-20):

/*
 * Motor control code for 5 motors on 2 stacked mtr shields
 * Listen on serial port for 6 comma separated integer values
 * First int value is a flag.
 * if flag == 0:  just send back sensor data
 * if flag == 1:  command 4 wheel motors with next 4 values
 * if flag == 2:  command lidar rotor motor with last value
 * regardless of flag value always send back sensor data
*/

#include <Wire.h>
#include <Adafruit_Sensor.h>
#include <Adafruit_HMC5883_U.h>
#include <Adafruit_MotorShield.h>
#define trigPin1 2
#define echoPin1 3
#define trigPin2 4
#define echoPin2 5
#define trigPin3 6
#define echoPin3 7

// Global variables needed by SR04 sensors
long duration, distance, RightSensor, FrontSensor, LeftSensor;

/* Create object anad Assign a unique ID to HMC5883L. */
Adafruit_HMC5883_Unified mag = Adafruit_HMC5883_Unified(12345);

// Global variables needed by lidar sensor
#define UL unsigned long
#define US unsigned short

// Initialize Adafruit motor shield (wheel motors)
Adafruit_MotorShield AFMS1 = Adafruit_MotorShield(0x61); 
Adafruit_DCMotor *mtr1 = AFMS1.getMotor(1); // mtr1 is a pointer
Adafruit_DCMotor *mtr2 = AFMS1.getMotor(2);
Adafruit_DCMotor *mtr3 = AFMS1.getMotor(3);
Adafruit_DCMotor *mtr4 = AFMS1.getMotor(4);
// another shield with up to 4 more motors
Adafruit_MotorShield AFMS0 = Adafruit_MotorShield(0x60); 
Adafruit_DCMotor *mtr5 = AFMS0.getMotor(1);
Adafruit_DCMotor *mtr6 = AFMS0.getMotor(2);
Adafruit_DCMotor *mtr7 = AFMS0.getMotor(3);
Adafruit_DCMotor *mtr8 = AFMS0.getMotor(4);

int mtr = 0;  // ?
int spd = 0;  // ?

void SonarSensor(int trigPin,int echoPin)
{
  digitalWrite(trigPin, LOW);
  delayMicroseconds(2);
  digitalWrite(trigPin, HIGH);
  delayMicroseconds(10);
  digitalWrite(trigPin, LOW);
  duration = pulseIn(echoPin, HIGH);
  distance = (duration/2) / 29.1; // cm
}

void CommandWheels(int spd1, int spd2, int spd3, int spd4)
{
  if (spd1 < 0) {
    mtr1->run(BACKWARD);
  }
  else {
    mtr1->run(FORWARD);
  }
  if (spd2 < 0) {
    mtr2->run(BACKWARD);
  }
  else {
    mtr2->run(FORWARD);
  }
  if (spd3 < 0) {
    mtr3->run(BACKWARD);
  }
  else {
    mtr3->run(FORWARD);
  }
  if (spd4 < 0) {
    mtr4->run(BACKWARD);
  }
  else {
    mtr4->run(FORWARD);
  }
  if (spd1 > 255) {
    spd1 = 255;
  }
  if (spd2 > 255) {
    spd2 = 255;
  }
  if (spd3 > 255) {
    spd3 = 255;
  }
  if (spd4 > 255) {
    spd4 = 255;
  }
  if (spd1 < -255) {
    spd1 = -255;
  }
  if (spd2 < -255) {
    spd2 = -255;
  }
  if (spd3 < -255) {
    spd3 = -255;
  }
  if (spd4 < -255) {
    spd4 = -255;
  }
  mtr1->setSpeed(abs(spd1));
  mtr2->setSpeed(abs(spd2));
  mtr3->setSpeed(abs(spd3));
  mtr4->setSpeed(abs(spd4));
}

void CommandRotor(int spd)
{
  if (spd < 0) {
    mtr7->run(BACKWARD);
  }
  else {
    mtr7->run(FORWARD);
  }
  if (spd > 255) {
    spd = 255;
  }
  if (spd < -255) {
    spd = -255;
  }
  mtr7->setSpeed(abs(spd));
}

// Split string into substrings, return substring by index
String getSubString(String data, char separator, int index) {
  int found = 0;
  int strIndex[] = { 0, -1 };
  int maxIndex = data.length() - 1;
  for (int i = 0; i <= maxIndex && found <= index; i++) {
    if (data.charAt(i) == separator || i == maxIndex) {
      found++;
      strIndex[0] = strIndex[1] + 1;
      strIndex[1] = (i == maxIndex) ? i+1 : i;
    }
  }
  return found > index ? data.substring(strIndex[0], strIndex[1]) : "";
}

void setup()
{
  Serial.begin(9600); // For communication w/ controlling computer
  Serial.setTimeout(10);
  while (!Serial) {
    ; // wait for serial port to connect.
  }
  Serial.println("Hello from Arduino :-)");
  Serial.flush();
  AFMS0.begin();
  AFMS1.begin();
  // use mtrx->setSpeed (not mtrx.setSpeed) because mtrx is a pointer
  mtr1->setSpeed(0); // wheel 1 motor
  mtr2->setSpeed(0); // wheel 2 motor
  mtr3->setSpeed(0); // wheel 3 motor
  mtr4->setSpeed(0); // wheel 4 motor
  mtr5->setSpeed(0);
  mtr6->setSpeed(0);
  mtr7->setSpeed(0); // lidar rotor
  mtr8->setSpeed(0);


  /* Initialize pins for ultrasonic sensors */
  pinMode(trigPin1, OUTPUT);
  pinMode(echoPin1, INPUT);
  pinMode(trigPin2, OUTPUT);
  pinMode(echoPin2, INPUT);
  pinMode(trigPin3, OUTPUT);
  pinMode(echoPin3, INPUT);
}
 
void loop() {
  // Get ultrasonic sensor data.
  SonarSensor(trigPin1, echoPin1);
  FrontSensor = distance;
  /*
  SonarSensor(trigPin2, echoPin2);
  LeftSensor = distance;
  SonarSensor(trigPin3, echoPin3);
  RightSensor = distance;
  */
  if (Serial.available() > 0) {
    // Read incoming string from RasPi
    String inString = Serial.readString();
    // send acknowledgement back to RasPi
    Serial.println("100,0,0");
    // Parse incoming data and command motors accordingly
    String str0 = getSubString(inString, ',', 0);
    String str1 = getSubString(inString, ',', 1);
    String str2 = getSubString(inString, ',', 2);
    String str3 = getSubString(inString, ',', 3);
    String str4 = getSubString(inString, ',', 4);
    String str5 = getSubString(inString, ',', 5);
    int flag = str0.toInt();
    int spd1 = str1.toInt();
    int spd2 = str2.toInt();
    int spd3 = str3.toInt();
    int spd4 = str4.toInt();
    int spd5 = str5.toInt();
    if (flag == 1)
    {
      CommandWheels(spd1, spd2, spd3, spd4);
    }
    if (flag == 2)
    {
      CommandRotor(spd5);
    }
  }
  //if (FrontSensor <= 10)
  //{
    //CommandWheels(0, 0, 0, 0);
  //}
}

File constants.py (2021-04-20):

# Car geometery parameters
W2W_DIST = 34  # separation between coaxial wheels (cm)
SONAR_LIDAR_OFFSET = 15  # offset distance between sonar & lidar

# Driving parameters
CARSPEED = 200  # default car speed
SONAR_STOP = 5  # threshold E-stop distance (cm) 
FWD = 3   # forward drive direction (with cross-track correction)
LFT = 90  # left drive direction
REV = 180  # reverse drive direction
RGT = -90  # right drive direction

# PID feedback related parameters
KP = 0.6  # steering PID proportional coefficient
KI = 0.1  # steering PID integral coefficient
KD = 1.5  # steering PID derivative coefficient
PIDTRIM = 12  # default value for spin trim
PIDWIN = 6  # number of values to use in rolling average

# Scan related parameters
LEV = 5000  # Low Encoder Value (45-deg behind car's -X direction)
HEV = 30000  # High Encoder Value (car +X direction)
VLEG = 3  # optical path length of vetical leg (cm)

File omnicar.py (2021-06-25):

"""This program accesses all the motors & sensors of the omni wheel car.

RasPi's USB serial port used to send motor drive cammands to Arduino.
BNO085 IMU attached on RasPi UART RX pin, sends heading data.
TFminiPlus lidar data attached to FT232 USB serial device.
Scan rotor angle encoder data via ADC on RasPi I2C bus.

See omni-wheels.md for an explanation of wheel motor drive.
"""
import logging
import math
import os
from pprint import pprint
import RPi.GPIO as GPIO
import serial
import smbus
import sys
import time
import Adafruit_ADS1x15
from adafruit_bno08x_rvc import BNO08x_RVC
from constants import LEV, HEV, VLEG, PIDTRIM
import geom_utils as geo
import pathfwd

logger = logging.getLogger(__name__)
logger.setLevel(logging.INFO)  # set to DEBUG | INFO | WARNING | ERROR
logger.addHandler(logging.StreamHandler(sys.stdout))

SECTOR_WIDTH = 18  # Minimum value for open sectors
RADIUS_FACTOR = 1.2  # Used when finding open sectors

# Adafruit BNO085 IMU
imuport = "/dev/serial0"
ser0 = serial.Serial(imuport, 115200, timeout=0.1)
logger.info(f"BNO085 IMU UART port = {imuport}")
rvc = BNO08x_RVC(ser0)

# Communication with Arduino
ports = ['/dev/ttyACM0', '/dev/ttyACM1', '/dev/ttyS0']
for port in ports:
    if os.path.exists(port):
        ser1 = serial.Serial(port, 9600, timeout=0.5)
        break
    else:
        port = None
logger.info(f"Arduino communication port = {port}")

# Lidar distance sensor
lidarport = '/dev/ttyUSB0'
ser2 = serial.Serial(lidarport, 115200)
logger.info(f"Lidar port = {lidarport}")

# 16 bit ADC (for odometer & lidar rotor encoder values)
i2cbus = smbus.SMBus(1)
adc = Adafruit_ADS1x15.ADS1115()

# GPIO pin setup
HDG_RESET_PIN = 18  # Broadcom pin 18 (Pi pin 12)
ODO_RESET_PIN = 24  # Broadcom pin 24 (Pi pin 18)
GPIO.setmode(GPIO.BCM)
GPIO.setup(HDG_RESET_PIN, GPIO.OUT)
GPIO.setup(ODO_RESET_PIN, GPIO.OUT)
GPIO.output(HDG_RESET_PIN, GPIO.HIGH)
GPIO.output(ODO_RESET_PIN, GPIO.HIGH)

def encoder_count_to_radians(enc_cnt):
    """
    Convert encoder count to angle (radians) in car coordinate system

    Lidar rotor angle encoder 0-5 V -> 0-2*pi radians
    encoder_count values start at 0 and increase with CW rotation.
    straight ahead (+X axis): enc_cnt = 20,000; theta = 0
    straight back (-X axis): enc_cnt = 0; theta = pi
    straight left (+Y axis): enc_cnt = 10,000; theta = pi/2
    straight right (-Y axis): enc_cnt = 30,000; theta = -pi/2
    (enc_cnt tops out at 32765, so no info past that)
    """
    theta = math.pi * (20000 - enc_cnt) / (20000)
    return theta


class OmniCar():
    """Control motors & access sensors of omni-wheel car.

    Also produce rotating scan with paired distance, angle values.
    """

    def __init__(self):
        self.distance = 0  # last measured distance (cm) from lidar
        self.points = None  # scan data (list of dictionaries)
        self.ODOMETER_OFFSET = 136
        

    @property
    def odometer(self):
        """Return odometer value in cm."""
        counts = adc.read_adc(1, gain=1, data_rate=250)
        # Formula below found empirically
        return int((counts - self.ODOMETER_OFFSET) * 0.0106)

    def reset_odometer(self):
        """Reset odometer to 0 cm."""
        # Ground the reset pin.
        GPIO.output(ODO_RESET_PIN, GPIO.LOW)
        time.sleep(0.05)
        GPIO.output(ODO_RESET_PIN, GPIO.HIGH)
        time.sleep(0.5)  # Wait before first reading
        test_val = adc.read_adc(1, gain=1, data_rate=250)
        readings = []
        for n in range(10):
            readings.append(adc.read_adc(1, gain=1, data_rate=250))
        avg_count = int(sum(readings) / len(readings))
        self.ODOMETER_OFFSET = avg_count
        logger.debug("Odometer reset to 0 cm")

    @property
    def heading(self):
        """Return instantaneous heading (gyro yaw) in degrees.

        BNO085 sends data @ 100 reading/sec on ser0 in RVC mode.
        yaw has a range of +/- 180˚ in 0.01˚ increments.
        """
        ser0.reset_input_buffer()  # purge stale data
        yaw, *_ = rvc.heading
        return yaw

    def reset_heading(self):
        """Reset heading to 0 degrees."""
        GPIO.output(HDG_RESET_PIN, GPIO.LOW)
        time.sleep(0.01)
        GPIO.output(HDG_RESET_PIN, GPIO.HIGH)
        time.sleep(0.5)  # to avoid read errors
        logger.debug("Heading reset to 0 degrees")
    
    def _read_serial_data(self):
        """Read and return one line from serial port"""
        in_string = None
        while not in_string:
            if ser1.in_waiting:
                in_bytes = ser1.readline()
                in_string = in_bytes.decode("utf-8").rstrip()
        return in_string

    def _xfer_data(self, send_data):
        """Xfer data to Arduino: Send motor spd values, get acknowledge
        send_data is a tuple of 6 integers: (flag, m1, m2, m3, m4, m5)
        flag = 0 (ignore motor values, just get sensor data)
        flag = 1 (apply motor values m1 thru m4 and get sensor data)
        flag = 2 (apply motor value m5 and get sensor data)"""
        # convert integers to strings for sending on serial
        send_data_str = (str(item) for item in send_data)
        logger.debug(f"Data to send: {send_data}")
        out_string = ",".join(send_data_str)
        out_string += '\n'
        logger.debug(f"String being sent: {out_string}")
        ser1.write(out_string.encode())
        # Receive acknowledgement
        snsr_str = self._read_serial_data()
        if not snsr_str:
            snsr_str = 'No sensor data'
        logger.debug(f"serial data read: {snsr_str}")
        return snsr_str

    def go(self, speed, angle, spin=0):
        """Drive at speed (int) in relative direction angle (degrees)
        while simultaneoulsy spinning CCW at rate = spin (int)."""

        # convert from polar coordinates to omni_car's 'natural' coords
        # where one coaxial pair of wheels drives u and the other drives v
        u, v = geo.p2r(speed, angle + 45)

        # motor numbers
        # m1, m2, m3, m4 = (1, 2, 3, 4)

        # combine motor speed with spin
        m1spd = int(spin + u)
        m2spd = int(spin - u)
        m3spd = int(spin - v)
        m4spd = int(spin + v)

        # friction keeps motors from running smoothly at speeds below ~50
        if 0 < m1spd < 50:
            m1spd = 50
        if 0 < m2spd < 50:
            m2spd = 50
        if 0 < m3spd < 50:
            m3spd = 50
        if 0 < m4spd < 50:
            m4spd = 50

        if -50 < m1spd < 0:
            m1spd = -50
        if -50 < m2spd < 0:
            m2spd = -50
        if -50 < m3spd < 0:
            m3spd = -50
        if -50 < m4spd < 0:
            m4spd = -50

        distances = self._xfer_data((1, m1spd, m2spd, m3spd, m4spd, 0))
        return distances
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

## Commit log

2020-11-03 Modified arduino scan function to not home rotor at end of scan, just stop.
2020-11-03 Revert "Modified arduino scan function to not home rotor at end of scan, just stop."
    This reverts commit 7af1f51078f191026b2b6f6972257d145b1923e1.
2020-11-03 tweaked some parameters in Arduino sketch
2020-11-05 Replaced multiple lists of point attrbutes with a single list of Point types
    [ztcar_w_lidar.py]
2020-11-17 documentation additions & revisions
    [ang_encdr_calibr.xlsx]
2020-11-26 Began converting to an Omni-wheel chassis.
2020-11-28 added rudimentary motor controls for wheels
2020-11-30 revised & renamed ztcar.py to omnicar.py, to accomodate chassis change.
2020-12-06 Discovered I had a bad motor shield so moved wheels to good shield. modified: motorControl/motorControl.ino modified: omnicar.py renamed: operate_wheels.py to operate_motors.py new file: trigger_shut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
2020-12-07 modified README.md to show LiDAR mounted on omni-wheel type car
2020-12-10 Moved documentation of omni-wheels from omnicar.py to omni-wheels.md
2020-12-10 Consolidated code in new file operate_car.py. Added trim parameter to make subtle steering changes.
2020-12-11 added separate coefficients kp and kd for PID steering, renamed the wheel drive commands.
2020-12-12 Added steering trim to more drive commands. Added govern method to ensure motor speed doesn't exceed 255. Added ability to confine scan to desired sector of interest.
    [omnicar.py, operate_car.py]
2020-12-12 The Omni-Wheel car has achieved its "Hello World!" milestone by demonstrating the ability (crudely) to find its way CCW around a rectangular object (a sofa).
2020-12-13 analyze_data revised to return mroe info. Added steering trim to remaining diagnal driving methods.
2020-12-21 Modified omnicar.py to read compass heading from HMC5883L device.
2020-12-21 added turn functions to use feedback from compass sensor.
2020-12-21 incorporate use of compass heading feedback to steer along target course.
2020-12-22 replaced map_scan_data.py with proscan.py which encapsulates scan map & analaysis in a class.
    [omnicar.py, operate_car.py, proscan.py]
2020-12-23 incorporated standard parameter names: lev & hev (low and high encoder values) for specification of sector of interest in both OmniCar.scan and ProScan().
2020-12-24 Added logging to operate.py to toggle printing of debug messages.
2020-12-25 Updated omni-wheels.md to show how to drive wheels at any arbitrary relative heading. Added go method to implement this, replacing existing methods to go_at 8 cardinal & intercardinal directions.
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2020-12-27 Fixed broken heading() method by moving read_raw_data() back inside class. Replaced round_corner() with turn() function, which incorporates compass feedback.
    [omnicar.py, operate.py]
2021-01-01 moved lidar to a usb serial port and changed RasPi-Arduino communications from SPI to Serial
    [HC-SR04_CC_mnt.dxf]
2021-01-02 modified approach and drive_along_wall to steer to compass heading rather than wall angle.
2021-01-02 Bi-directional communication (RasPi/Arduino) working over serial bus with motor commands sent to Arduino and sonar sensor data sent back to RasPi.
2021-01-03 mostly debugged after installing sonar sensor on front of car and changing Arduino communications from SPI to serial.
2021-01-10 modified motor-control to stop wheels when front_dist < 10 cm. Began using scan data more strategically, rather than for navigation. Use scan data to find best open path forward.
2021-01-10 Consolidated encoder calibration values (LEV, MEV, HEV) in omnicar.
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2021-01-13 fixed logging in proscan; adjusted LEV, HEV to get walls to align to grid; adjusted GAP, CORNER; use GAP value adjusted for distance.
    [omnicar.py, operate.py, proscan.py]
2021-01-17 fixed bug in _find_corners
    [proscan.py]
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2021-01-18 Added 'lidar_issues' to docs. Explains tests of diffferent modules connected to different serial ports.
    [scan_data0.csv, scan_data1.csv, scan_data2.csv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]
2021-01-19 modified: motorControl/motorControl.ino to remove e-stop at frontSensor < 10 added more tty device options to omnicar consolidated saving of data into save_scan function in operate
2021-01-20 Revised lidar issues documentation to show results of new read_dist method.
2021-01-21 Thinning triplicate points no longer needed.
    [omnicar.py, operate.py, proscan.py]
2021-01-21 fixed the way segments are found in regions. enabled optional numbers to be applied to save data filenames.
    [omnicar.py, operate.py, proscan.py]
2021-01-24 replaced test.py with remap.py minor revisions operate.py
    [omnicar.py, operate.py, remap.py]
2021-01-24 Added VLEG constant to account for optical path length of vert leg. Adjusted LEV & HEV constants to align scanned walls to grid in plot.
2021-01-25 omnicar: Added OmniCar.resync to resynchronise reads of the LiDAR data when it gets out of step. operate: Added FWD, REV, RGT, & LFT constants for driving in cardinal directions. proscan: Fixed typo 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
    [omnicar.py, operate.py, proscan.py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]
2021-01-26 Revised drive_along_wall_to_right to use lidar for cross-track & angle feedback. Move saved data to a 'Data' folder.
2021-01-26 Modified approach_wall. Previously used sonar distance for closed loop feedback. Now stop point is dead reckoned from distance to scan line. For some reason, the sonar data looks to be much cleaner n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
2021-01-31 Improvements to driving along wall: ETA class to improve stopping resolution, adjust EOW, gap, fit. approach now includes backing away if too close.
    [operate.py, proscan.py, remap.py]
2021-02-03 Replaced Point class with dictionary.
    [operate.py, proscan.py]
2021-02-03 Previously, car Y axis was aimed at the wall as it drove_along_wall_to_right. This has now been revised to keep car Y axis pointing along travel path as it drives_along_wall_on_left. Works OK but cou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
2021-02-07 Calibrated HMC5883L (compass), including elaborate documentation.
    [compass-data.csv, compass-data.xlsx]
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2021-02-12 Revised corner finding to reduce the possibility of finding 'false' corners within a region. Corners list now includes both region start index and region end index. Added class DeltaT for examining e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
    [operate.py, proscan.py]
2021-02-12 operate.py: Added automatic plot updates at end of run. Misc fixes related to lev, hev.
    [omnicar.py, operate.py, proscan.py]
2021-02-13 Replaced turn_on_the_go with bevel turn at corner. More accurate.
    [operate.py]
2021-02-13 created 2 versions of function drive_ahead() (one with PID steering, one w/out). Created interactive fuction drive_to_spot displaying interactive plot to allow tele-op control.
2021-02-14 Added function get_rates() to calculate driving rate (cm/sec) for different speeds. Revised PID to avoid the 0/360 transition. Changed some PID coefficients to improve performance of drive_to_spot().
    [operate.py]
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2021-02-24 Revisions to enable drive_ahead(dist) to provide reaonable odometry while working without closed-loop compass feedback.
2021-03-04 Incorporated magnetic deviation at third of three stopping points along test route, consisting of a zig-zag sequence of drives and turns. Scan points were plotted overlayed on map after each drive or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
2021-03-19 Added 2 IMU's: mpu6050 on I2C bus and BNO085 on UART in RVC mode.
2021-03-20 Replaced HMC5883L & MPU6050 devices. Replaced with BNO085 device operating in uart-RVC mode. Revised all associated code.
    [omnicar.py]
2021-03-20 Added code (and a wire) to enable reset heading to zero.
    [omnicar.py]
2021-03-25 Tweaked print statements to facilitate copy-paste to .md format.
2021-03-28 Added plotting of waypoints in trip. Fixed non-normalized values of Trip.drive_angle to be between +/- 180.
    [mapper.py]
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2021-04-09 Removed unused code from proscan2.py, other minor fixes.
    [constants.py, omnicar.py, proscan2.py]
2021-04-12 Added odometer (wheel encoder). Incorporated into Trip class. Noticed that ablity of car to turn in place has been adversely affected.
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2021-04-12 WheelEncoder.ino revised to stop/start data flow on command from RasPi.
2021-04-16 Odometer data now comes to RasPi through ADC, previously through USB serial.
2021-04-16 Fixed car.heading by adding a 1 second delay at the end of reset_heading
    [omnicar.py]
2021-04-20 Renamed operate2.py to operate.py and revised the way polar coordinate angle theta (which is pos CCW) interoperates with car.heading (which is pos CW). Previously the Trip class had its own 'hdg' var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
    [constants.py, operate.py]
2021-04-24 Added function drive_ahead(dist) to pid steer to maintain zero heading error. Added PID class. Revised Trip.drive_to_target to incorporate pid steering.
    [omnicar.py, operate.py]
2021-04-27 OmniCar.reset_odometer self-tests and corrects to null value.
    [omnicar.py, operate.py]
2021-05-07 Increased delay time after odometer reset to fix occasionally resetting to -50 cm.
    [omnicar.py, operate.py]
2021-05-10 Modified Trip to save scanpoints from each leg.
2021-05-16 Added pathfwd module for analyzing scan points to find best path forward, avoiding any obstructions in the way. Uses cv2 and numpy.
    [omnicar.py, operate.py, pathfwd.py]
2021-05-16 Removed no longer used old code for calculating target point in open sector. Also removed code for plotting and saving scan points.
    [omnicar.py, operate.py]
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
